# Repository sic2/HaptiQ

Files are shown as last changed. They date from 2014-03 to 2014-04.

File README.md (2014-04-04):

### HaptiQ: A Haptic Device for Graph Exploration by People with Visual Disabilities

**Student:** Simone Ivan Conte

**Supervisor:** Miguel A. Nacenta

# Project Description:

Traditional touchscreen devices do not provide any tactile feedback, being then of scarce usability for people with visual disabilities.
Miguel A. Nacenta and his team at the University of Calgary, now a Lecturer in St Andrews, developed the Haptic TableTop Puck (HTP), an inexpensive tactile feedback input device to be used on digital tabletop surfaces. Friction, height, texture, and malleability are communicated through a combination of properties of the HTP: a rod and a brake pad controlled by two servo motors, and a pressure sensor on the rod. The HTP, however, uses only one actuator on a finger to convey information to the user, which makes it unsuitable for use by people with visual disabilities, since people cannot detect directions and edges of tactile objects.

The aim of this project is to extend the HTP concept and overcome some of its limitations for its use for people with visual disabilities. The extension will consist into using multiple servo motors and rods as well as redesigning the API to support new functionalities (haptic objects, behaviours, etc).
 
My hypothesis is that the HaptiQ (pronounced Haptic cue) will facilitate the recognition of directions and edges of displayed objects. The first main objective is to create a physical prototype that is adapted for the specific needs of people with visual disabilities. 

-------------------------------------------------------------------------------

# Objectives

## Primary
    - Design and implement an haptic device for graph exploration by people with visual disabilities.
    - Develop an API to control one or more haptic devices.
    - Develop an API to easily develop WPF client applications.
    - Design and implement a new set of dynamic behaviours.
    - Design and implement a basic application for Graphs exploration.

## Secondary
    - Increase the haptic device resolution.
    - Allow the haptic device to provide audio-feedback as well.
    - Design and implement an application for simple mathematical functions exploration.

## Tertiary
    - Enable the haptic device to be used collaboratively.
    - Enable the haptic device to sense textures.

# Hardware used

- Phidgets ServoBoard and InterfaceKit
- Phidgets Servo Motors
- Pressure Sensors
- 3D-Printed models 

# Collaborating

This project is currently under alpha development and the designing is constantly changing.

Please do create a branch of the project if a new feature has to be implemented. Also, use the issue tracking on GitHub if any bug is found or new functionality is wanted.

## Getting started

Please refer to the manual to get started with the HaptiQ and the HaptiQ API

## Bugs
Whenever a bug is found please: 
- Assign a short, clear and meaningful name to the bug
- Be precise and clear
- Include only one problem per report

And follow a similar scheme

    +-------------+---------------------------------------------------+
    | Description | Describe the issue (step by step)                 |
    | Workaround  | Explain a way to temporarily solve the problem    |
    | Solution    | Explain what the solution should be               |
    | Attachments | Attach any relevant Log/Screenshot file if needed |
    +-------------+---------------------------------------------------+
    Label: bug, duplicate, invalid, etc..

# Acknoledgments

This work is supported by the School of Computer Science of the University of St Andrews and SISCA

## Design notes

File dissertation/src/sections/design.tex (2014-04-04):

\chapter{Design}

The HaptiQ aims to solve some of the problems identified in the related work. The hardware was developed using an iterative exploratory process. Therefore the design phases largely overlap with the implementation ones. The API provided has also undergone through many iterations. In this chapter I will first discuss the earliest prototypes. Then the 4-HaptiQ and the 8-HaptiQ hardware designs are illustrated. Finally, a detailed overview of the API is provided.

\section{The Hardware}
\subsection{Early Prototypes}
The hardware design of the HaptiQ has been initially based on the HTP design. Similarly to the HTP, the HaptiQ also uses mini-servos to control its actuators. However, while the HTP controls only one actuator, the HaptiQ controls four or eight of them. It immediately follows that as the number of actuators increases, so does the number of servos and the size of the device. In order to minimise the size, I designed three main prototypes by sketches (see Figure ~\ref{fig:HaptiQ-early-prototypes}). 

The first prototype extends the rotational axis in the xy plane (see Figure ~\ref{fig:first prototype}). The extension is designed as a gear that allows to choose combinations of three aligned actuators. An additional actuator would then be used to raise the selected actuators. This design reduces the number of servos, but all raised actuators will have the same height. Note that the focus of this design sketch was to minimise the number of servos, that is why actuators are shown as points, similar to Braille displays.

\begin{figure}
        \centering
        \begin{subfigure}[H]{0.5\textwidth}
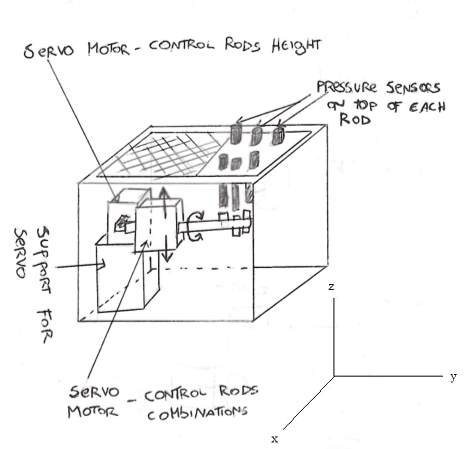
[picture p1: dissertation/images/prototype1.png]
                
                \caption{Grid based}
                \label{fig:first prototype}
        \end{subfigure}%
        ~ %add desired spacing between images, e. g. ~, \quad, \qquad etc.
          %(or a blank line to force the subfigure onto a new line)
        \begin{subfigure}[H]{0.5\textwidth}
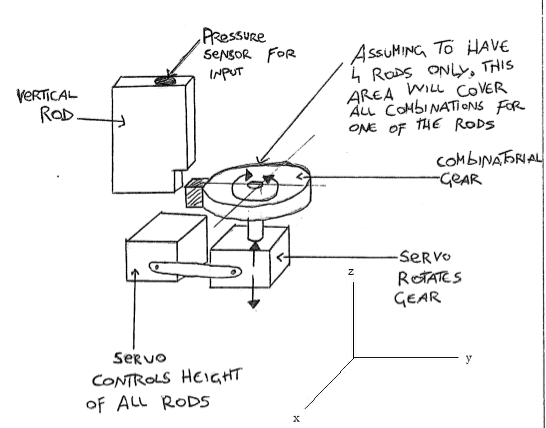
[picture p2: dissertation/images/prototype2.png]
                
                \caption{Gear based}
                \label{fig:second prototype}
        \end{subfigure}
        ~ %add desired spacing between images, e. g. ~, \quad, \qquad etc.
          %(or a blank line to force the subfigure onto a new line)
        \begin{subfigure}[H]{0.5\textwidth}
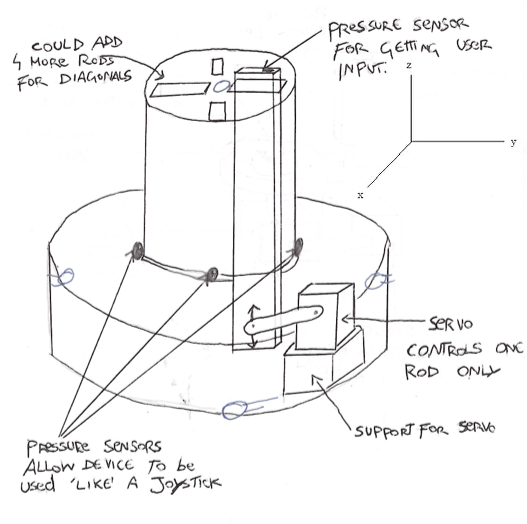
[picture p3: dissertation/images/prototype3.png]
                
                \caption{One servo per actuator}
                \label{fig:third prototype}
        \end{subfigure}
        \caption{HaptiQ early prototypes}\label{fig:HaptiQ-early-prototypes}
\end{figure}

In the second prototype I tried to minimize the total number of servos to two. One servo would be used to rotate a combinatorial gear about the z-axis (see Figure ~\ref{fig:second prototype}). A second servo can then be used to raise the first servo and all the rods. This approach can be considered very versatile and could allow an high number of actuators by keeping the number of servos always to two. Nonetheless, the actuators would all be at the same height when raised as in the first prototype. Since height can be used to convey additional information, this prototype was discarded and a third prototype was created.

The third prototype does not focus on minimising the number of servos any more, but rather on the possible functions that could be added to the HaptiQ. In this design each servo controls an actuator only and these are disposed circularly around the centre of the device (see Figure ~\ref{fig:third prototype}). The device would have a \textit{joystick} shape. Three pressure sensors could be added either at the bottom of the device or in between the internal and the external annuli. Using simple triangulation on the pressure sensors values, it could be possible to use the device like a gaming joystick and eventually augment its area of interaction. However, in one of the meetings with Saad, we realised that blind people would find this feature disrupting because understanding how far in the xy plane the device is augmented can become a challenging task. 

\subsection{4-HaptiQ}
The 4-HaptiQ is the first functional HaptiQ. This is an experimental project, with future work discussed in chapter 9, so I will occasionally refer to the device with the term prototype. This version has four actuators as shown in Figure ~\ref{fig:HaptiQ reference static actuators}. Unlike the third of the early prototypes, the main focus is on the mechanics and functions aspects.
The most successful aspect of the HTP, most probably, is the use of a small servo to mechanically move the rod along the z-axis. Nonetheless, the mechanic design used in the HTP has some flows that the HaptiQ tries to solve. The HTP, in fact, transforms the rotational motion of the servo to a linear motion only by ensuring that the servo works under a small range and that the rod slices outside the device through a small opening.
In the HaptiQ the actuators slide through a guide that allows motion only in the z-direction. In addition, each servo is linked to its actuator by using one or more screws inserted in between small openings in the actuator (see Figures ~\ref{fig:HaptiQ MinPos} and ~\ref{fig:HaptiQ MaxPos}). 

\begin{figure}
        \centering
        \begin{subfigure}[H]{0.3\textwidth}
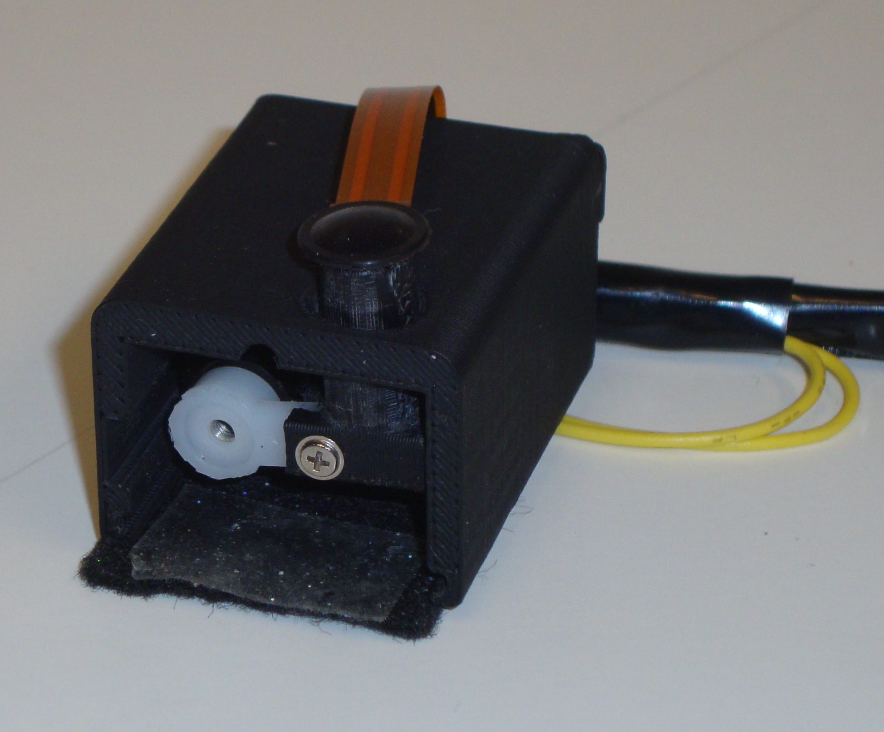
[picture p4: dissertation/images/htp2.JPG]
                
                \caption{HTP}
                \label{fig:Mechanics HTP}
        \end{subfigure}%
        ~ %add desired spacing between images, e. g. ~, \quad, \qquad etc.
          %(or a blank line to force the subfigure onto a new line)
        \begin{subfigure}[H]{0.3\textwidth}
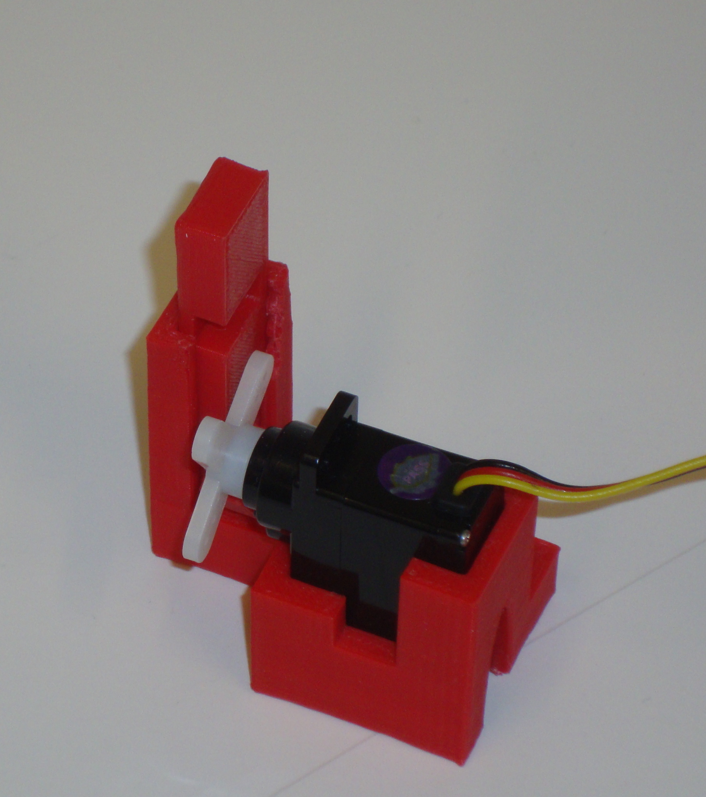
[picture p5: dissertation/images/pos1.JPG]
                
                \caption{HaptiQ MinPos}
                \label{fig:HaptiQ MinPos}
        \end{subfigure}
        ~ %add desired spacing between images, e. g. ~, \quad, \qquad etc.
          %(or a blank line to force the subfigure onto a new line)
        \begin{subfigure}[H]{0.3\textwidth}
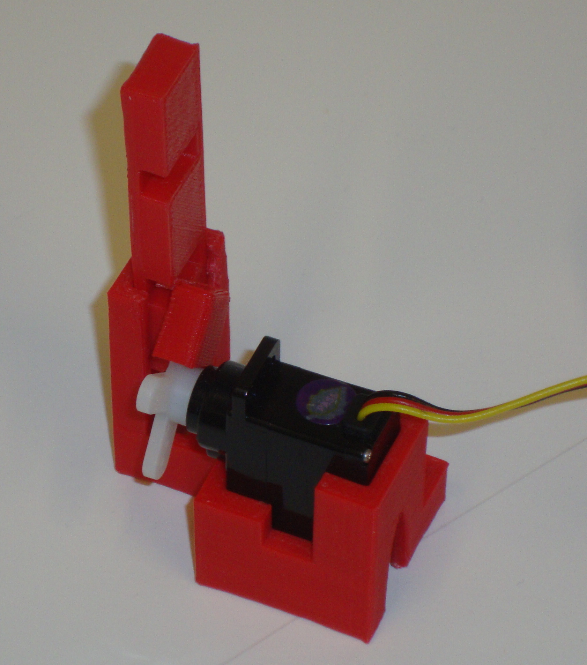
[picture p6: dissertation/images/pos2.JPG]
                
                \caption{HaptiQ MaxPos}
                \label{fig:HaptiQ MaxPos}
        \end{subfigure}
        \caption{HTP and HaptiQ actuator mechanics}\label{fig:HTP and HaptiQ actuator mechanics}
\end{figure}

This version of the HaptiQ does not provide any case. The uneven surface leads to the lack of a reference point or plane for the actuators. This is a major problem in cases where the actuators change position while the user is not currently laying his hand on the device. In fact, it follows that when the blind user places the hand on top of the device again, he or her is not able to tell what the current state of the actuators is compared to the previous one. Two solutions are provided for the 4-HaptiQ: a mid-point reference and a plane reference static actuators (see Figure ~\ref{fig:HaptiQ reference static actuators}). It is not clear which type of reference actuator works best though. My hypothesis is that the plane reference actuator should be more comfortable when using the device and provides the same functionality than the point reference actuator. 

\begin{figure}
        \centering
        \begin{subfigure}[H]{0.5\textwidth}
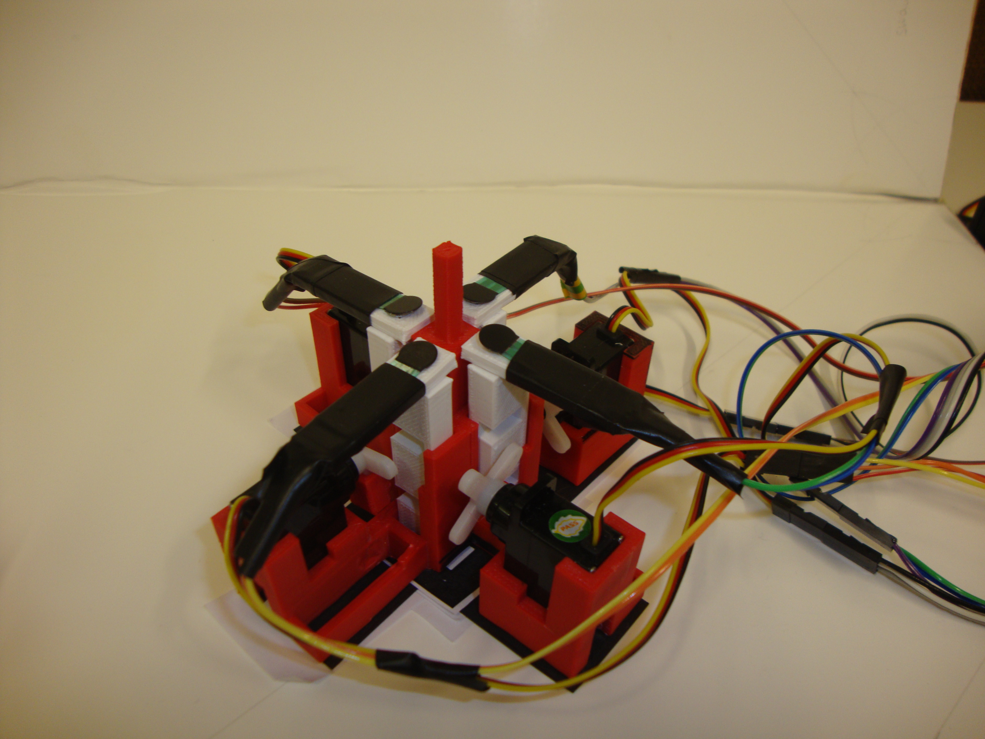
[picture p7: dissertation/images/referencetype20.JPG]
                
                \caption{Mid-Point reference actuator}
                \label{fig:Mid-Point reference actuator}
        \end{subfigure}%
        ~ %add desired spacing between images, e. g. ~, \quad, \qquad etc.
          %(or a blank line to force the subfigure onto a new line)
        \begin{subfigure}[H]{0.5\textwidth}
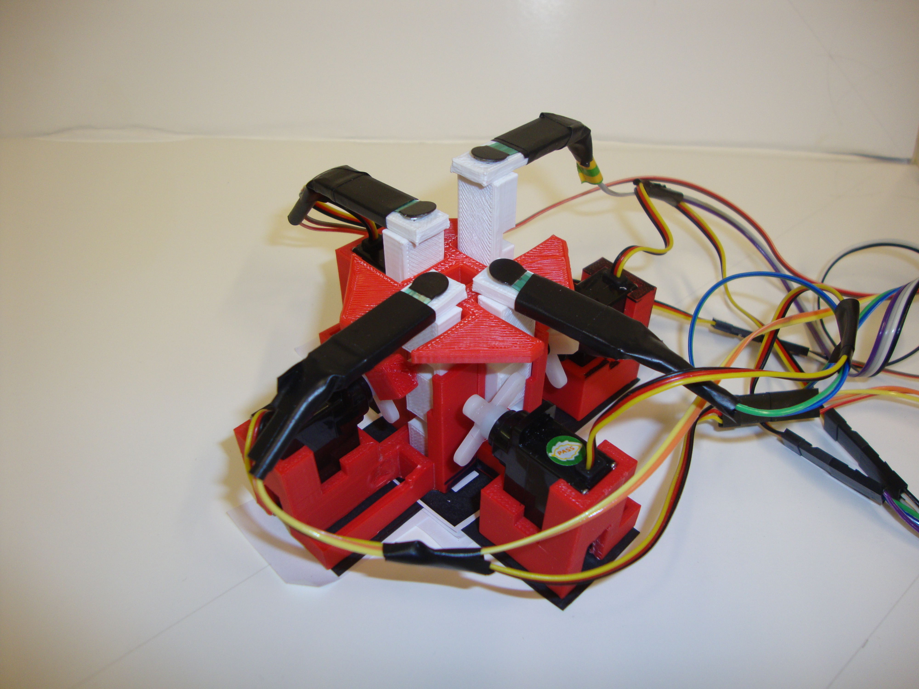
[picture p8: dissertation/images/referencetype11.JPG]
                
                \caption{Plane reference actuator}
                \label{fig:Plane reference actuator}
        \end{subfigure}
        ~ %add desired spacing between images, e. g. ~, \quad, \qquad etc.
        \caption{HaptiQ reference static actuators}\label{fig:HaptiQ reference static actuators}
\end{figure}

The HaptiQ is the first vector-based display for blind users. Whether this design provides better feedback to users or not is unknown, because no study with participants could be conducted. Therefore, the actuators are designed so to support different tops in order to be able to evaluate the HaptiQ against a point-based haptic feedback TUI. In the version here presented, only vector-like tops are provided, but other type of tops can be easily printed and fasten to the actuators.   

Finally, the HaptiQ does not have any break to simulate friction. While it could be possible to add this feature, I decided that the primary goal of this project was just to focus on the \textit{vectorisation} of the actuators. 

\subsection{8-HaptiQ}
The result of the final design iteration is the 8-HaptiQ. Using the same design of the 4-HaptiQ for eight actuators would lead to a considerable increase in size of the device. Therefore, the 8-HaptiQ has been completely re-engineered (see Figure ~\ref{fig:8-HaptiQ}). 

\begin{figure}[H]
  \centering
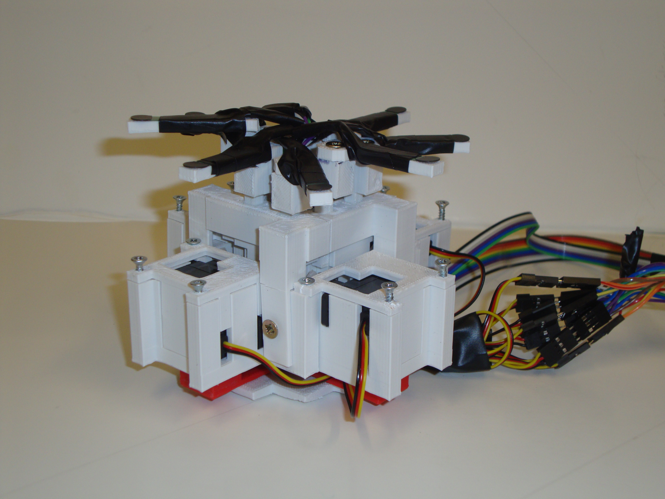
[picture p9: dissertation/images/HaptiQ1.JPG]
  
  \caption{8-HaptiQ}
  \label{fig:8-HaptiQ}
\end{figure}

The 4-HaptiQ not only is not optimised in terms of space, but its wiring is also not well engineered. As it is possible to observe in Figure ~\ref{fig:HaptiQ reference static actuators} the wiring does not allow the device to be used comfortably, especially when one wants to rotate it. 
The servos in the 8-HaptiQ are organised in couples. Unlike its predecessor, the servos are positioned horizontally (see Figure ~\ref{fig:8-HaptiQservos}) and the screws are moved more toward the centre of the rotatory mechanism of the servos. These design choices allow the device to be more compact and still preserve the same functionalities of the 4-HaptiQ. 
The device is lift up by an additional structure laying below it, allowing the wiring to be less disruptive. 

\begin{figure}[H]
  \centering
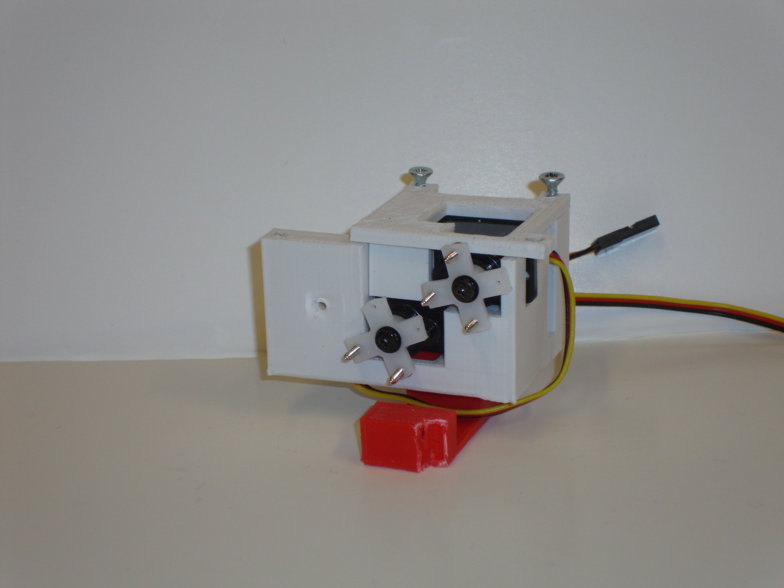
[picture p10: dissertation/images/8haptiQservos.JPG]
  
  \caption{8-HaptiQ servos couple}
  \label{fig:8-HaptiQservos}
\end{figure}

With the gathering of the wires for the sensors to the center of the device, the position of the sensors is also inverted compared to the 4-HaptiQ. While in the 4-HaptiQ the sensors meet in the middle, with this new version of the HaptiQ they are spread to the outside. It is not clear whether this design choice is an advantage or not in terms of usability. Alternatives to this solution will be provided in the near future, as discussed in the Future Work chapter.

The 8-HaptiQ takes a different approach for the design of the actuators guides. In the first version, a base was provided for the actuator, which limits this to move further down when this is at its minimum position (see Figure ~\ref{fig:HaptiQ MinPos}). But to provide an optimal wiring, the 8-HaptiQ combines the guides for all the actuators with the reference plane (see Figure ~\ref{fig:8haptiqref}). Additional connecting screws allow the actuators to be always controlled by the servos and not to fall below its minimum position. 

\begin{figure}[H]
  \centering
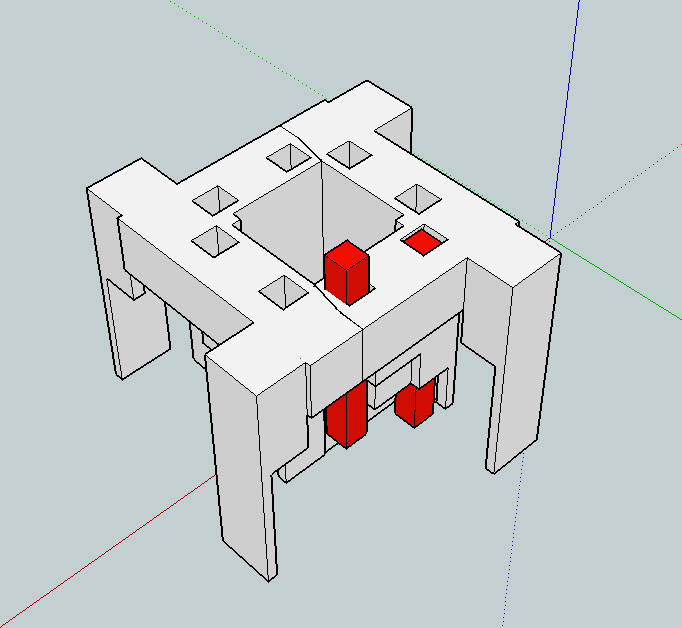
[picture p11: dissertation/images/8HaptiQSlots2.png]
  
  \caption{8-HaptiQ reference plane and actuators slots}
  \label{fig:8haptiqref}
\end{figure}

\subsection{Fiducial Markers}

The HaptiQ, like the HTP, is designed to work on interactive tabletops, specifically on Microsoft PixelSense tables (supporting Microsoft Surface SDK 2.0) \footnote{Microsoft. \url{http://www.pixelsense.com/}. [Online; last checked: 26/04/2014].}. The Microsoft Surface Bytetag is the standard fiducial marker for the PixelSense tables (see Figure ~\ref{fig:Bytetag}). But Bytetags are hard to print, if high accuracy is wanted, and expensive, if one wants to buy them from the official store.

The HaptiQ, in addition to the  Microsoft Bytetags, supports glyphs, as defined by the Glyph Recognition And Tracking Framework (GRATF)\footnote{GRATF. \url{http://www.aforgenet.com/projects/gratf/}. [Online; last checked: 04/04/2014].} (see Figure ~\ref{fig:glyph}).

Both types of fiducial markers are to be displaced on the bottom of the device, if a PixelSense table (or equivalent) is used. Otherwise, it could be possible to place a glyph on top of the device, provided that an appropriate structure is built, and recognise it using a web-cam. 

\begin{figure}[H]
        \centering
        \begin{subfigure}[H]{0.2\textwidth}
                
                \caption{Bytetag}
                \label{fig:Bytetag}
        \end{subfigure}%
        ~ %add desired spacing between images, e. g. ~, \quad, \qquad etc.
          %(or a blank line to force the subfigure onto a new line)
        \begin{subfigure}[H]{0.2\textwidth}
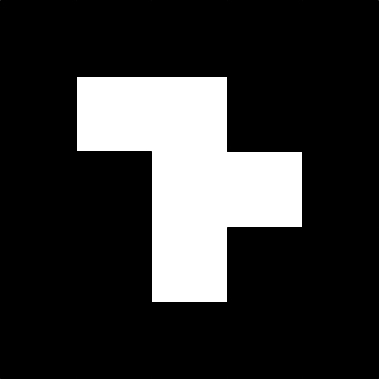
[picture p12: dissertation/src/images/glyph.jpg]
                
                \caption{Glyph}
                \label{fig:glyph}
        \end{subfigure}
        ~ %add desired spacing between images, e. g. ~, \quad, \qquad etc.
        \caption{Fiducial Markers}
        \label{fig:fiducialMarkers}
\end{figure}

\section{The API}

This section discusses the design choices taken for the API of the HaptiQ. The general idea is similar to the HapticTouch toolkit \cite{ledo2012haptictouch}. However, this has been completely redesigned to support:

\begin{itemize}
	\item multiple actuators
    \item multiple pressure sensors
    \item a completely new approach to HapticObjects and HapticBehaviours
    \item custom actions called when input is received by the user
    \item additional API to get input position of the device from different hardware
\end{itemize}

Each of these will be discussed in the following sections. 

\subsection{Overall Structure}

The API consists of two main components: the HaptiQ API used to control the device and the Input API (see Figure ~\ref{fig:api}). 
The HaptiQ API component is designed to provide high and low access to the HaptiQ. This allows the API to be versatile and to be used by beginner, intermediate and advanced developers. 
The HaptiQ API retrieves the position of the device through the Input API. 

The following two sections describe these components in more details.

\begin{figure}[H]
  \centering
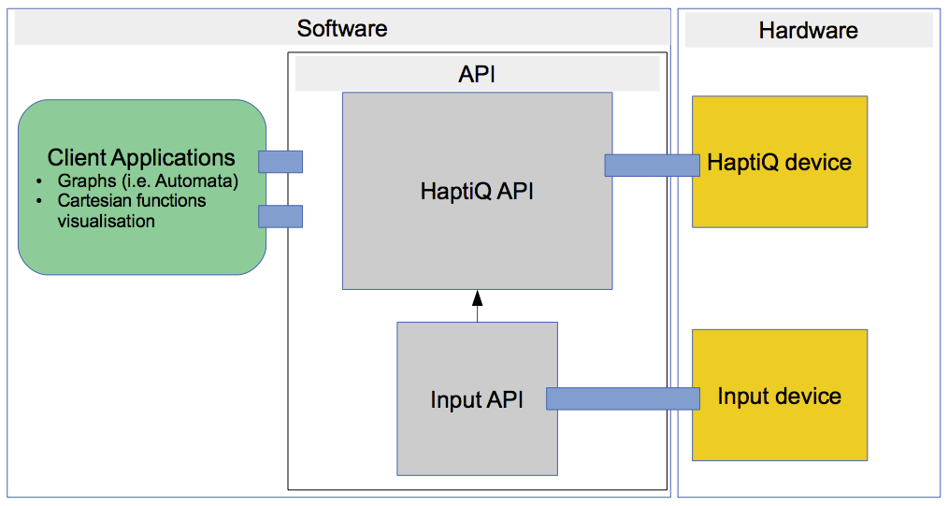
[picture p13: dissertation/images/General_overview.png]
  
  \caption{API General Overview}
  \label{fig:api}
\end{figure}

\subsection{Input API}

Initially, the HaptiQ, like the HTP, was designed to work on a Microsoft PixelSense table only.
Microsoft Surface Bytetags are located underneath the HTP to get the location of the device in the table. However, official Bytetags are expensive and printing them with a normal printer does not lead to satisfying results. In addition, the HaptiQ will be used in the near future on digital tables that do not support the Surface SDK. Therefore, in order to abstract the HaptiQ API from any hardware input dependence, a separate API component has been created (see Figure ~\ref{fig:input_api}). 

The architectural structure of the Input API is based on the classic Factory pattern. This adds a level of abstraction over the hardware that should be used to get the position of the HaptiQ. Currently the API supports Bytetags and glyphs recognition. But client applications can also add their own customised class to support different position detection methods. 

\begin{figure}[H]
  \centering
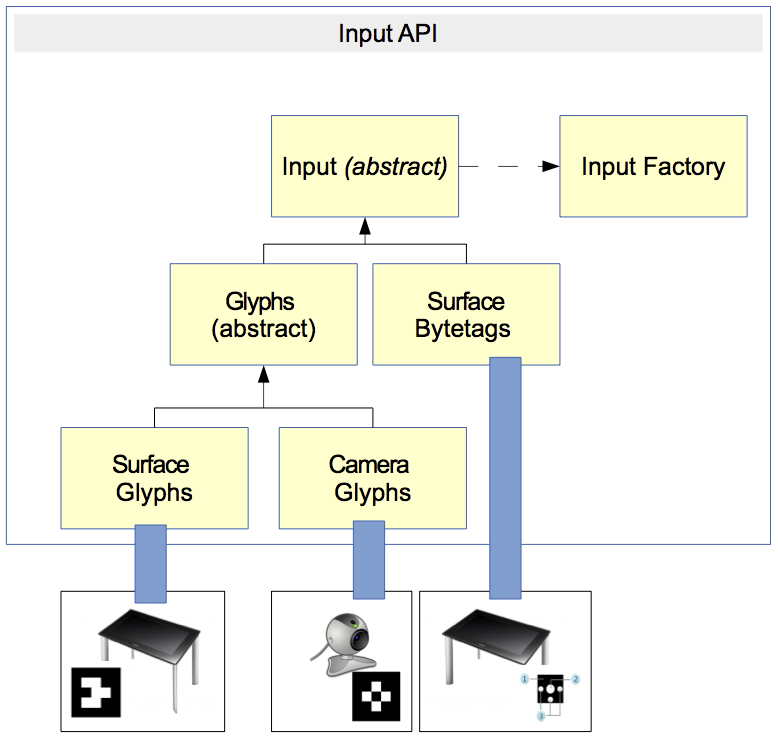
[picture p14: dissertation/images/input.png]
  
  \caption{Input API}
  \label{fig:input_api}
\end{figure}

\subsection{HaptiQ API}

The HaptiQ API plays the main role within the API by connecting the Input API, the HaptiQ device and the client applications all together (see Figure ~\ref{fig:haptiQ_api}). 

The HaptiQsManager is designed using the Singleton pattern, ensuring that only one instance exists, and controls the different parts of the internal structure of the HaptiQ API. On creation, the manager launches the configuration manager. At this stage, the API looks in the current directory for pre-saved configurations of HaptiQs. If there are not valid configurations matching the current attached devices to the machine, a configuration windows form is started, allowing users to set up devices. Otherwise, HaptiQ objects are created for each configured device. 

Each HaptiQ is a thread process on its own, which runs the current behaviours cyclically. The HaptiQ class is responsible both for controlling the actuators and getting the input via the pressure sensors. 

The manager, however, is responsible to get the devices position through the Input API. Using the observer pattern, the HapticObjects registered by the client applications are notified whenever a new input is received. If the input is relevant to a particular HapticObject, then a behaviour is returned to the HaptiQ device that caused it. 

The API allows behaviours to be added, removed, and substituted. This means that the current state of a device can be the combination of multiple behaviours. This adds an extra dimension to the haptic cues that can be transferred to the user. 

On the other hand, each HaptiQ can keep track of pressure events, without the intervention of the HaptiQsManager. Pressure data events are automatically fired to registered HapticObjects. Each HapticObject reacts differently to pressure input. 

\begin{figure}[H]
  \centering
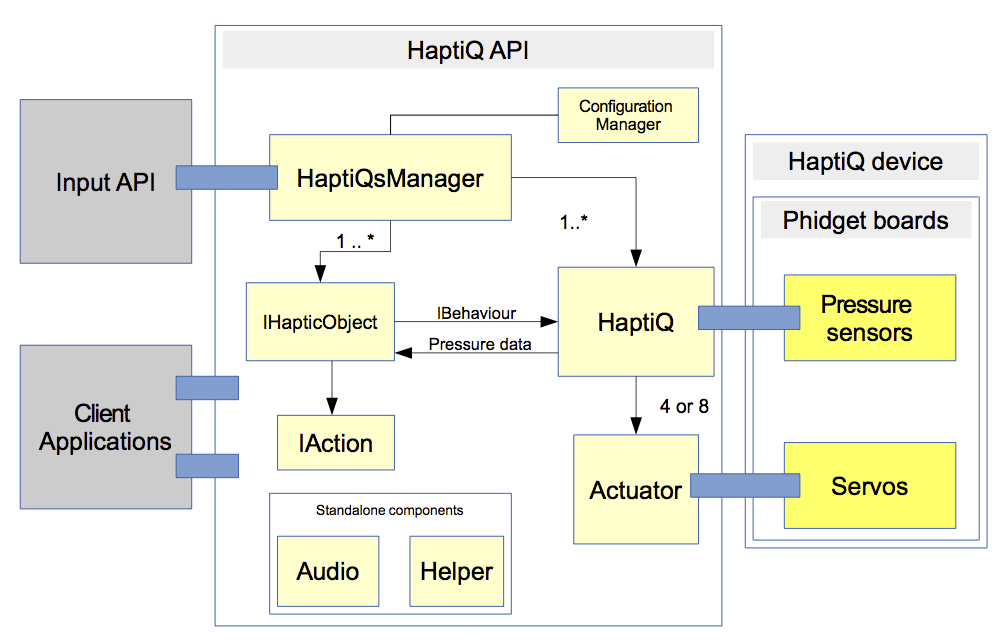
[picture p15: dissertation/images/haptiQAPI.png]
  
  \caption{HaptiQ API}
  \label{fig:haptiQ_api}
\end{figure}

\subsubsection{Haptic Objects}
Basic haptic objects are provided by the API and are designed to be used by WPF (Windows Presentation Foundation) applications without having to concern about behaviours and additional low level mechanisms. All haptic objects can carry textual information. In fact, applications should prioritise the information one wants to convey, rather than the aesthetics of the objects. Therefore, only simple shapes are provided. Obviously, one can extend the HapticShape abstract class to provide more interesting shapes, but this is outside the scope of this project.

Haptic objects are the main visual components of the client applications. Therefore, clients can also register custom actions to be run when pressure events are received by a specific object.

Figure ~\ref{fig:hapticObjects} shows examples of the haptic objects supported by the API. Rectangles and circles can be used as identity objects (e.g. nodes in a graph). Identity objects can also be linked. Links can have directions (from red to green) or not. The API allows also to specify lines and polylines. One of the example applications provided with the API, for example, uses polylines to display mathematical functions.

The used Fiducial Markers do not provide very precise input location of the device. In order to compensate, the HapticObjects provided are extended (red borders in Figure ~\ref{fig:hapticObjects}). This makes it harder to the user to leave the object, compensating for the inaccuracy of detecting the device location.

\begin{figure}[H]
        \centering
        \begin{subfigure}[H]{0.4\textwidth}
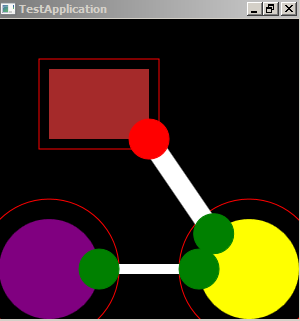
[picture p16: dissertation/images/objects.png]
                
                \caption{Identity objects and links}
                \label{fig:objects1}
        \end{subfigure}%
        ~ %add desired spacing between images, e. g. ~, \quad, \qquad etc.
          %(or a blank line to force the subfigure onto a new line)
        \begin{subfigure}[H]{0.4\textwidth}
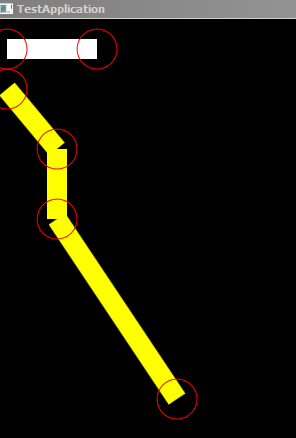
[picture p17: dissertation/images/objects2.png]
                
                \caption{Line objects}
                \label{fig:objects2}
        \end{subfigure}
        ~ %add desired spacing between images, e. g. ~, \quad, \qquad etc.
        \caption{Haptic Objects}\label{fig:hapticObjects}
\end{figure}

\subsubsection{Audio Feedback}

The audio component is a standalone one, allowing any part of the API, as well as client applications, to output beeps or textual information as audio.

While this is a small component, it still plays an important role in the API. Ungar and Blades \cite{ungar2000can} discuss whether the conjoint retention hypothesis, combining spatial and linguistic information, can provide richer haptic cueing. Their study did not show any significant improvement when adding audio feedback. However, they results were not definitive. Therefore, I decided to follow the trend of many commercial applications, like VoiceOver, which use audio to provide textual and position feedback too.

In the API provided, the Beep feedback is used only for HapticLines and HapticPolylines. The reason is that following lines is harder than identifying the existence of shapes. This approach is similar to the one taken in audio feedback applications, such as VoiceOver.

The speech synthesiser, instead, is used to read out textual information stored in the HapticObjects.

\section{Tactons}
\label{sec:designTactons} 

Pietrzak et al. \cite{pietrzak2009creating} propose a set of tactons that can be used on pin array devices and that could be used to indicate edges and directions. These tactons are designed for a $4 \times 4$ pins grid. The HaptiQ provides a maximum of eight actuators, uses lines rather than points to convey haptic cues and can provide height information as well (pin arrays typically provide only 0/1 information). Here, I present a new set of tactons. From this section on, the terms tacton and behaviour will be used interchangeably.

A tacton is used by an HapticObject to notify a device how to react when this is located on top of it. In the provided API there is a strong relationship between each HapticObject and a behaviour. Nonetheless, behaviours can be used by client defined HapticObjects or directly from a client application.

In the following sections, the scales in Figure ~\ref{fig:scales} will be used to represent the heights of the actuators.

\begin{figure}[H]
        \centering
        \begin{subfigure}[H]{0.7\textwidth}
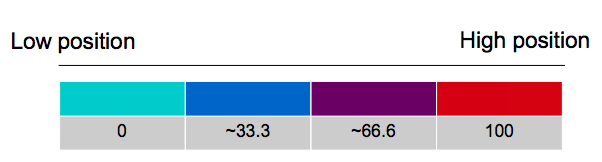
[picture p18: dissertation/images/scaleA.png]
                
                \caption{4-HaptiQ}
                \label{fig:scale-4}
        \end{subfigure}%
        ~ %add desired spacing between images, e. g. ~, \quad, \qquad etc.
          %(or a blank line to force the subfigure onto a new line)
          
        \begin{subfigure}[H]{0.7\textwidth}
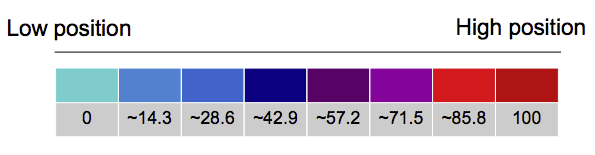
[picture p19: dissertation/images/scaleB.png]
                
                \caption{8-HaptiQ}
                \label{fig:scale-8}
        \end{subfigure}
        ~ %add desired spacing between images, e. g. ~, \quad, \qquad etc.
        \caption{Blue-Red scale used to indicate the height of the actuators in tactons diagrams. Numerical values represent the positions of the actuators in percentage}
        \label{fig:scales}
\end{figure}

\subsection{Flat and Max}

Flat and Max are the simplest tactons of the set (see Figure ~\ref{fig:Basictactons}). The Flat tacton is typically used to indicate that underneath the device there are no objects or information. The Max behaviour, instead, can be used to represent the existence of an object. For instance, when the device is inside an HapticRectangle the Max behaviour is played. 

\begin{figure}[H]
  \centering
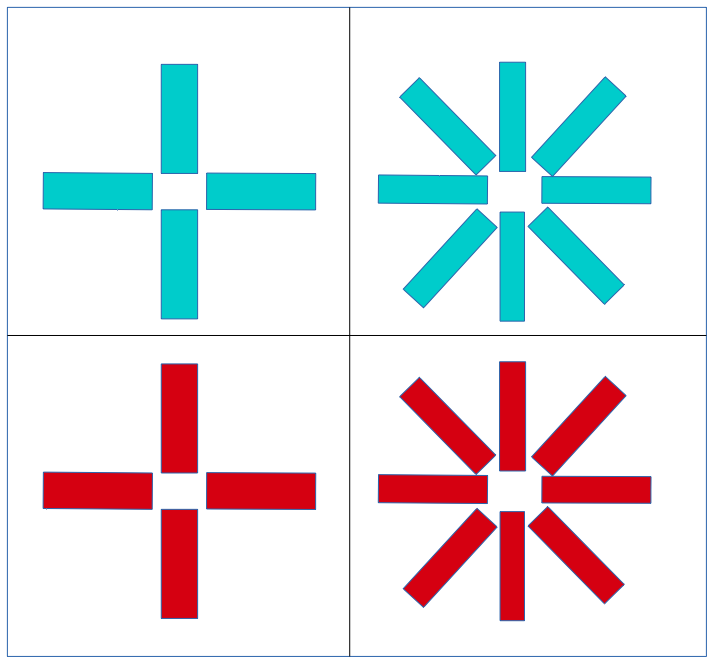
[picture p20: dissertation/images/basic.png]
  
  \caption{Basic tactons: Flat and Max}
  \label{fig:Basictactons}
\end{figure}

\subsection{Notification}
\label{sec:notification}

The Notification tacton, similarly to the Max tacton, can also be used to notify an object. In the case being, this tacton is used to notify an HapticCircle. This tacton consists into cyclically changing the positions of the actuators (see Figure ~\ref{fig:notification}). Each rod always increases or decreases its height position. But in the case the maximum or minimum height threshold is reached, the actuator direction (increase or decrease in height) is inverted.

\begin{figure}[H]
        \centering
        \begin{subfigure}[H]{0.7\textwidth}
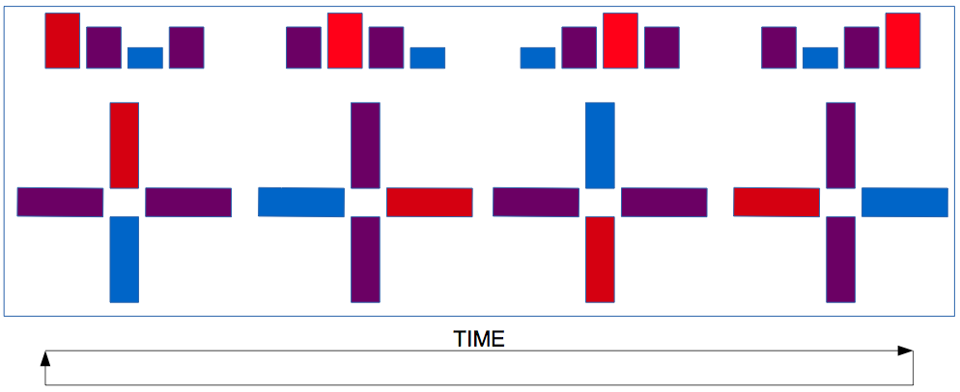
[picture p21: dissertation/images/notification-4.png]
                
                \caption{4-HaptiQ}
                \label{fig:notification-4}
        \end{subfigure}%
        ~ %add desired spacing between images, e. g. ~, \quad, \qquad etc.
          %(or a blank line to force the subfigure onto a new line)
          
        \begin{subfigure}[H]{0.7\textwidth}
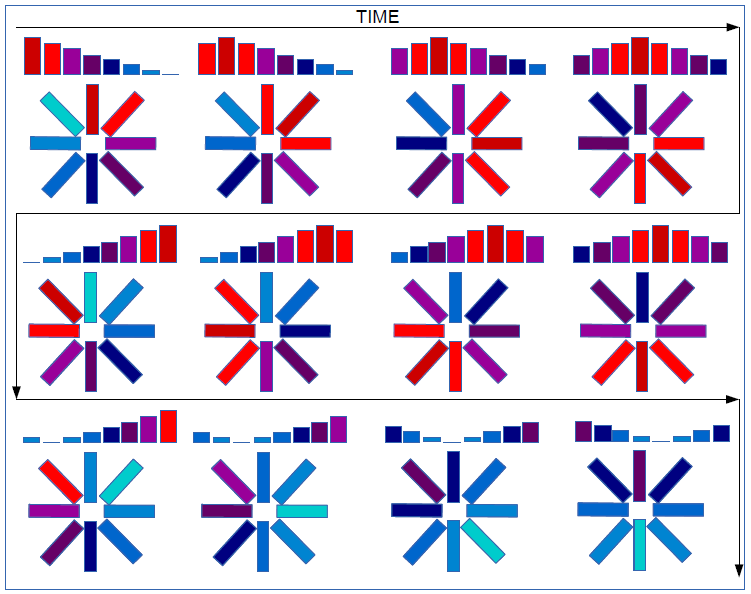
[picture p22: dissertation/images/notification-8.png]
                
                \caption{First 12 cases for 8-HaptiQ}
                \label{fig:notification-8}
        \end{subfigure}
        ~ %add desired spacing between images, e. g. ~, \quad, \qquad etc.
        \caption{Notification tacton}\label{fig:notification}
\end{figure}

\subsection{Edges and Corners}

The Edge-Corner tacton is probably the most significant one of all the tactons by allowing users to perceive edges and corners. 

Figure ~\ref{fig:edges} show how the combinations of actuators, in both the prototypes, are used to represent edges. The resolution of the device is increased by alternatively actuating adjacent actuators. It is possible to achieve a precision of 45° and 22.5° for the 4-HaptiQ and the 8-HaptiQ respectively. 

\begin{figure}[H]
        \centering
        \begin{subfigure}[H]{0.3\textwidth}
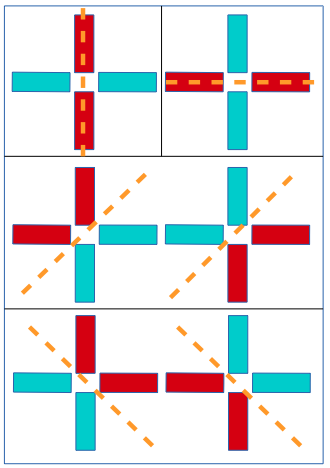
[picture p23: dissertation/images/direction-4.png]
                
                \caption{4-HaptiQ}
                \label{fig:direction-4}
        \end{subfigure}%
        ~ %add desired spacing between images, e. g. ~, \quad, \qquad etc.
          %(or a blank line to force the subfigure onto a new line)
        \begin{subfigure}[H]{0.5\textwidth}
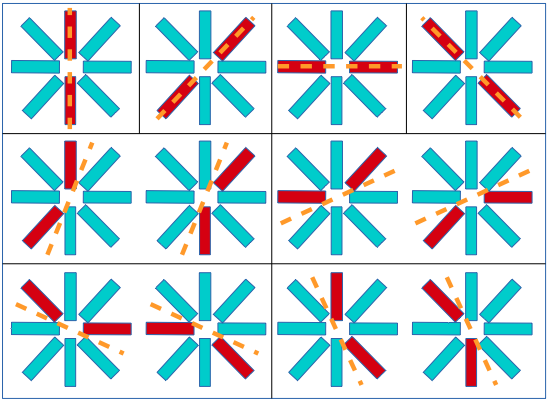
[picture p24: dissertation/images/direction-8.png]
                
                \caption{8-HaptiQ}
                \label{fig:direction-8}
        \end{subfigure}
        ~ %add desired spacing between images, e. g. ~, \quad, \qquad etc.
        \caption{Edge tacton patterns}\label{fig:edges}
\end{figure}

It is also possible to represent corners, which are merely the combinations of two edges. The 4-HaptiQ can represent corners of 90° with a precision of 45° (see Figure ~\ref{fig:corner-4}). Indeed, the 8-HaptiQ can represent corners of 45°, 90° and 135°, with a precision of 22.5° (see Figures ~\ref{fig:corner-8}, ~\ref{fig:corner-8c}). 

\begin{figure}[H]
        \centering
        \begin{subfigure}[H]{0.5\textwidth}
                
                \caption{4-HaptiQ}
                \label{fig:corner-4}
        \end{subfigure}%
        ~ %add desired spacing between images, e. g. ~, \quad, \qquad etc.
          %(or a blank line to force the subfigure onto a new line)
          
        \begin{subfigure}[H]{0.4\textwidth}
                
                \caption{8-HaptiQ}
                \label{fig:corner-8}
        \end{subfigure}
        ~ 
         \begin{subfigure}[H]{0.5\textwidth}
                
                \caption{8-HaptiQ (combinations)}
                \label{fig:corner-8c}
        \end{subfigure}
        ~ %add desired spacing between images, e. g. ~, \quad, \qquad etc.
        \caption{Corner tacton patterns}\label{fig:corners}
\end{figure}

The Edge-Corner tacton is used by the HapticRectangle, to represent its borders, and the HapticLine and HapticPolyline objects. 

\subsection{Pulsation and Linear}
The Pulsation and Linear tactons are used with the HapticLink to represent the sign of the link between two Haptic objects. Figure ~\ref{fig:pulsation} shows two cases of the pulsation tacton for the 4-HaptiQ. By symmetry it is possible to represent 8 (or 16 for the 8-HaptiQ) directions. This tacton also allows frequency to be specified, so that pulsation increases as one gets closer to the target. The static actuators in this tacton are also fundamental to identify orientation of the direction.

The Linear tacton, on the other hand, is the union of the pulsation tactons, but without any pulsation behaviour. Thus, the height of the actuators is used rather than the pulsation frequency in order to convey different information about a direction. For example, the tacton can be encoded so that the height of the actuators increases linearly as the distance between the device and the target approaches zero.

\begin{figure}[H]
  \centering
  
  \caption{Pulsation tacton patterns}
  \label{fig:pulsation}
\end{figure}

\section{Applications}

The HaptiQ can provide a new set of haptic cues which allow the visually impaired to better perceive lines, edges and directions. The two example applications shown below illustrate the types of applications that can be created using the HaptiQ API. Note that these applications have been designed as proof-of-concepts and not as applications ready to be deployed to the end users.

\subsection{Graph Visualiser}
\label{sec:graphVis}

The first application is a basic graph visualiser. The application is designed to be used by people with visual disabilities, with the assistance of a person with normal or corrected vision. The assistant can create graphs using the provided graphical user interface (see Figure ~\ref{fig:graphsVis}). Graphs contain identity objects and links as well as lines and polylines. \\
In order to create new object, the assistant has to select one of the options on the left hand side. A new window will be prompted asking for the properties of the haptic object. The procedure is the same for all the objects, except for links where the user has to select which objects to link by physically touching the objects with a finger or a bytetag. 

The design is not complete, since it does not allow objects to be deleted and graphs to be saved for later use. However, this is a good example of a possible application for the HaptiQ. One of the issues raised by Saad, in fact, is that blind people have difficulties in visualising graphs such as finite automata, trees, or network topologies. 

\begin{figure}[H]
  \centering
  
  \caption{Graph Visualiser}
  \label{fig:graphsVis}
\end{figure}

\subsection{Function Visualiser}
\label{sec:funcVis}

The second application that this project uses to prove the flexibility and usability of the HaptiQ and its API is a function visualiser. One of the most challenging tasks for the visually impaired is to be able to \textit{visualise} mathematical functions. The design of the function visualiser is also very simple. The user inputs a function, as text, and the application then evaluates and displays it (see Figure ~\ref{fig:funcVisualiser}). The application uses haptic lines and polylines to represent the functions. Cartesian axes are also added for completeness.

\begin{figure}[H]
        \centering
        \begin{subfigure}[H]{0.4\textwidth}
                
                \caption{Linear function}
                \label{fig:funct1}
        \end{subfigure}%
        ~ %add desired spacing between images, e. g. ~, \quad, \qquad etc.
          %(or a blank line to force the subfigure onto a new line)
        \begin{subfigure}[H]{0.4\textwidth}
                
                \caption{Sine function}
                \label{fig:funct2}
        \end{subfigure}
        \caption{Function Visualiser}
        \label{fig:funcVisualiser}
\end{figure}

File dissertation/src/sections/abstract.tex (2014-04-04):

\section{Abstract}

Today's technology is not as accessible for blind and visually impaired people.
Overcoming this digital divide gap for people with visual disabilities is one of today's most overlooked challenges.
Current technology provides either expensive or non-flexible devices. This dissertation investigates both commercial devices commonly used by visually impaired people, and the state of the art of haptic feedback devices.

This project presents the first vector-based display with haptic-audio feedback for people with visual disabilities: the HaptiQ. 
Two different devices of varying resolution were 3D-printed as prototypes.
In addition, a general easy-to-use API is provided together with two basic example applications. The first application shows how the HaptiQ can be used to explore simple graphs. The second program instead displays mathematical functions and is used to show how the HaptiQ facilitates edge recognition.
The sets of behaviour patterns used so far are heavily based on the use of Braille-like systems. 

With this project a new set of dynamic behaviour patterns is visually encoded in a way which favours the recognition of edges, corners and directions.

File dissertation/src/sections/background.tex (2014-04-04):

\chapter{Background}

The following chapter presents the state of the art in haptic feedback technologies and the current commercial technology for the visually impaired. The related work taken into consideration is taxonomised based on how the various techniques and devices work and how users interact with them.

Research in haptic perception and visualization has grown significantly in the last 25 years \cite{roberts2007we}. Being able to cover most of the work in haptics is not feasible. Therefore, only the most significant related work to this project will be addressed.

\section{Commercial technology for the visually impaired}
The devices and techniques currently available on the market and used by most of the visually impaired differs from what researchers have been able to achieve in the last decade. The main reason is that the most advanced technology produced by researchers is either expensive or still a prototype, or both. 

Traditional Braille and tactile maps are by far the most intuitive and easy-to-use ways to access textual and graphical information. However, these approaches are static and do not allow access to electronic devices. The resolution of tactile maps is usually low, since font size tends to be large and zoom-in actions are not allowed. Dynamic Braille displays \cite{HumanWare, shimada2010development, blindMaps} allow traditional techniques to be used for technological devices. However, only a small portion of the display can be covered using these devices and being able to keep track of the current position within the display becomes challenging.

The auditory system for blind people is probably the most important of their senses. Using the tactile system to perceive the surrounding world, in fact, can be hard to learn, especially for people who become blind in their adult stage of their life. Screen readers, like JAWS\cite{JAWS}, or auditory-aiding software, like VoiceOver\cite{voiceOver}, allow the visually impaired to explore textual information and navigate maps as well. Systems that rely just on audio feedback allow a user to follow lines and directions by emitting sounds at different frequencies. It obviously follows that a user needs to constantly explore the area around a specific point in the map in order to perceive the direction of a line or understanding the shape of an object.    
    
\section{Multimodal Interactive Maps}
An attempt to allow blind people to access geographical maps through digital devices is via multimodal interactive maps (MIMs). MIMs are input-output devices that can make use of different technologies to allow users to access or insert information (i.e Input: speech recognition, touch input. Output: audio, tactile feedback). The work presented by Broke et al \cite{brock2010usage} is the most recent type of MIM, to my knowledge. People who are visually impaired usually tend to use all their fingers when exploring objects. Therefore, enhancing multitouch input allows users to perceive maps with greater ease. Nonetheless, the maps have to be printed for each new visualisation. 

\section{Tangible User Interfaces with Mechanical Actuators}
Haptic feedback devices that use mechanical actuations are becoming increasingly popular. In fact, these are usually more flexible and adaptable to displays of different sizes. They also provide better tactile cues than audio-based techniques and MIMs.

The first device to take in consideration is the Haptic Tabletop Puck (HTP)\cite{marquardt2009haptic}, which the HaptiQ can be considered the successor of. The HTP is a simple, inexpensive and small haptic device that suits particularly well for use on digital tabletop surfaces. The tactile cue, however, is applied through one single point only. The HTP has not been designed specifically for visually impaired people. Therefore, it is not very suitable for more complex tasks such as recognising a line or a direction and follow it. 

This type of problem has been observed also with the SensAble PHANToM\cite{massie1994phantom, yu2001haptic}. Participants were asked to follow one or more lines. But the experiment showed negative results, since having only one point contact did not allowed the participants to well understand the shape of the line, especially at the end points or corners. Similarly to users of VoiceOver, blind people using the PHANToM or the HTP need to guess the direction of lines and eventually randomly explore the surrounding. 

Harrison and Hudson \cite{harrison2009providing} propose dynamically changeable physical buttons that use either pneumatic actuation or Shape Memory Materials to enhance displays with tactile feedback. This type of displays is proved to be cheap, easy to produce and effective. They are also convenient for static public displays (i.e. ATMs) or cars panel control, but not for more generic displays, such as tabletops, since specific masks need to be created for each visualisation. 

Recently the Tangible Media Group, MIT, has presented the inFORM system, a 2.5D shape display that uses mechanical actuators to provide feedback to the user\cite{follmer2013inform}. Top-down projection and a Kinect are used to provide visual feedback and acquire user input. inFORM provides excellent haptic feedback and equivalent responsiveness, nonetheless the table is bulky and expensive.

\section{Haptic Feedback by alternative mediums}

Recently Bau et al. presented TeslaTouch\cite{bau2010teslatouch} and REVEL\cite{bau2012revel}, two haptic feedback systems based on electrovibration and reverse electrovibration respectively. The purpose of these systems is to create Augmented Reality Tactile displays. These could be both extrinsic, integrated in the environment, or intrinsic, augmenting the user. A study on visually impaired people, using the TeslaTouch, has also been conducted \cite{xu2011tactile}. Participants found hard to recognise dots, as used in Braille, especially due to the fact that the tactile feedback is perceived only when the finger moves. Straight lines could be recognised, allowing some shapes be perceived (circle, square and triangle), but not with accurate precision. Another limitation of vibrotractile based devices is that it cannot be used by multiple users concurrently. 

Other techniques used to improve haptic feedback on touchscreens rely on electromagnetism. FingerFlux \cite{weiss2011fingerflux} uses magnets attached on fingertips to provide ``attraction, repulsion, vibrations and directional haptic feedback'' in a table with electromagnets pixels. The main issue related to FingerFlux is that the resolution of the display cannot be increased over a certain threshold, otherwise the electromagnets interfere with each other. In addition, FingerFlux allows to create horizontal forces, but it is not possible to render sharp surfaces.    

UltraHaptics provides multi-point haptic feedback above an interactive surface using acoustic radiation force to generate haptic cues on targets in mid-air \cite{carter2013ultrahaptics}. The system has been shown to be fairly accurate and easy to use, yet accuracy degrades quickly as the user's hand is above 200mm. 

Haptic feedback can also be transmitted by ejecting air at high pressure. AIREAL is a scalable, inexpensive and practical system that uses air to augment reality of interactive surfaces and environments \cite{sodhi2013aireal}. AIREAL works well within gaming environments and haptic cues of external environments, but the low resolution limits its use for objects and edge recognition, especially for the visually impaired.

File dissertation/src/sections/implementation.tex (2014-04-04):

\chapter{Implementation}

This chapter provides an overview of the important implementation details about the HaptiQ, as described in the Design chapter. 
Firstly, the hardware implementation is discussed, followed by the API. A dedicated section will discuss the tactons implementation. Finally, implementation details about the two example applications are covered in the last section of this chapter.

\section{The Hardware}

Building the hardware components of the two HaptiQ devices has been a challenge on its own. Both the 4-HaptiQ and the 8-HaptiQ are 3D-modelled using Google Sketchup \footnote{Google SketchUp. \url{http://www.sketchup.com} . [Online; last checked: 03/04/2014].}. Models are then exported in the STL format, a standard in CAD software, and commissioned to a 3D printer. I used a MakerBot\textregistered   Replicator\texttrademark 2x. This is an experimental 3D printer, therefore high precision (\textless 2mm) is hard to achieve and requires many attempts before being able to print the wanted model. 

Phidgets boards\footnote{Phidges. \url{http://www.phidgets.com/} . [Online; last checked: 04/04/2014].} are used to control the micro servomotors, \textit{Hitech HS-65MG}\footnote{HITECH RCD USA. \url{http://hitecrcd.com/} . [Online; last checked: 04/04/2014].}, and get pressure inputs, via force-sensing resistors. The wiring is more of a demanding task, rather than a challenging one, requiring many hours of work.

The different components of the device are assembled using super glue and screws (see the HaptiQ manual for more information on printing and assembling the device). 

\subsection{Fiducial Markers}

The provided API supports the recognition of two types of fiducial markers: Microsoft Bytetags and GRATF glyphs. The HaptiQs, built for this project, place the fiducial markers on the bottom side. However, in the case of the the GRATF glyphs, the fiducial marker can also be placed on top of the device. This is true if we assume that an appropriate structure around the HaptiQ is built, and a web-cam or similar is used to retrieve top-view images of the device with the glyph.

\begin{figure}
        \centering
        \begin{subfigure}[H]{0.3\textwidth}
                
                \caption{Raw image of Hand}
                \label{fig:rawHand}
        \end{subfigure}%
        ~ %add desired spacing between images, e. g. ~, \quad, \qquad etc.
          %(or a blank line to force the subfigure onto a new line)
        \begin{subfigure}[H]{0.3\textwidth}
                
                \caption{Raw image of 4-HaptiQ with Glyph - type 1}
                \label{fig:rawHaptiQ1}
        \end{subfigure}
        ~ %add desired spacing between images, e. g. ~, \quad, \qquad etc.
          %(or a blank line to force the subfigure onto a new line)
        \begin{subfigure}[H]{0.3\textwidth}
                
                \caption{Raw image of 4-HaptiQ with Glyph - type 2}
                \label{fig:rawHaptiQ2}
        \end{subfigure}
        \caption{Raw images}\label{fig:rawImages}
\end{figure}

The Bytetags, according to Microsoft, can be printed on standard office paper \footnote{MSDN. Printing Tagged Objects. \url{http://www.msdn.microsoft.com/en-us/library/ee804862(v=surface.10).aspx/}. [Online; last checked: 04/04/2014].}. However, during the first iteration phase of this project it was evident that printed Bytetags lead to poor results, with the fiducial markers being tracked at low frequency.

The alternative solution is to use glyphs. The Surface SDK 2.0 allows to retrieve raw image data from the interactive table. Having access to this data, it is possible to apply classical image matching algorithms to identify particular objects. This is achieved using GRATF, a C\# library that allows recognition and localization of glyphs in still images. 

Figure ~\ref{fig:rawImages} shows three raw images retrieved through the Surface SDK 2.0. The Microsoft PixelSense uses near-infrared sensors. Figure ~\ref{fig:rawHand}, for instance, represents how the hand absorbs infrared light, rather than its heat values as one may think. Glyphs are $n \times n$ grids, with n from 5 to 8, where each cell is either black or white (see Figure  ~\ref{fig:glyph}) and minimum side length of 8mm, that can be printed using Glyph Recognition Studio \footnote{Glyph Recognition Studio. Available at \url{http://www.aforgenet.com/projects/gratf/}. [Online; last checked: 04/04/2014].}. Additional rules apply, such that that the border cells can only be white and the glyph cannot be symmetrical in any of its axis. The base of the HaptiQ is covered with white paper, so that the black tiles in the glyphs are recognised more easily (see Figure ~\ref{fig:rawHaptiQ1}). However, this is not sufficient for the glyph to be recognised at all angles. After testing glyphs of different dimensions and on different surfaces, I found out that extending the glyph with low absorption material (e.g. white foam board) improves the recognition of the glyph significantly (see Figures ~\ref{fig:rawHaptiQ2} and ~\ref{fig:whitesurface}).   

\begin{figure}[H]
  \centering
  
  \caption{HaptiQ with extended white board base}
  \label{fig:whitesurface}
\end{figure}

\section{The API}

\subsection{Input API}

The Input API is the component used to retrieve the HaptiQ location on the tabletop. It follows that this is highly hardware dependent on the used hardware, especially on the type of interactive surface. The current targeted hardware comprehends the Microsoft Tabletops using the Surface SDK 2.0. Code to retrieve image data from web-cams is also provided. 
As explained in the design section, two main classes exist in the Input API: one to recognise Bytetags and one to recognise glyphs.

Recognising the Bytetags is straightforward. This is done through the \textit{TouchTarget} object of the \textit{Microsoft.Surface.Core} library. On the other hand, glyphs are recognised by calling the \textit{FindGlyphs} function, from the GRATF library, on a bitmap image. GRATF does not provide any functionality to estimate the position and the rotation of the glyphs. However, when a glyph is recognised, all its vertices are known. The position is estimated by calculating the crossing point between the two diagonals of the glyph. The rotation, instead, is estimated using the inclination angle of one of the edges of the glyph. 

The API raises events of the form:
\lstset{style=sharpc1}
\begin{lstlisting}
delegate void ChangedEventHandler(object sender, InputIdentifier inputIdentifier, Point point, double orientation, EventArgs e);
\end{lstlisting}

in order to notify the current location of a device, recognisable by a unique identifier (Bytetag or glyph). Then the HaptiQsManager, from within the HaptiQ API, handles such events.  

It is important to note that Bytetags are supported for debugging purposes only. Working with the provided tabletop is time consuming. Allowing Bytetags to be used, it is possible to run, debug and test the system using the Input Simulator provided with the Surface SDK 2.0 using a normal machine. 

\subsection{HaptiQ API}

The HaptiQ API, as previously stated, controls the device and coordinates its work with the other two main components: the Input API and the applications. The \textit{HaptiQsManager}, the \textit{HaptiQ}, and the \textit{Actuator} classes play the major role in controlling the devices and ensuring the coordination between input locations, haptic objects and behaviours. These three classes are also dependent on the Phidget library \footnote{Phidgets. Library available at \url{http://www.phidgets.com/}. [Online; last checked: 04/04/2014].}. 

On the creation of the manager, the configuration process is launched (see section ~\ref{sec:configuration} for more details about devices configuration) and HaptiQ instances are created appropriately. The manager assigns each device a unique ID, which can be used to find and access a device. 
Each HaptiQ keeps track of its own actuators, the connected pressure sensors, and the current behaviours to play. After an HaptiQ instance is initialised in the constructor, an independent thread is initiated. This consists of a loop that runs all the current behaviours every 10ms. Reducing the frequency gradually decreases the smoothness of the played dynamic behaviours. On the other hand, increasing the frequency creates an unnecessary overuse of resources. 

A behaviour consists of a dictionary mapping an actuator of the device to its wanted position. The position is expressed as a value between 0 and 1, where 0 indicates that the actuator should be moved to its minimum position, and 1 to its maximum position. The manager retrieves behaviours to be played, from each haptic object, and distributes them to the devices that generated them. Nonetheless, an HaptiQ instance allows behaviours to be explicitly added or removed, giving more flexibility to clients. Similarly to the HTP toolkit, behaviours can be combined by averaging the positions for each actuator. 
Actuators are independent from each other, therefore it is possible to exploit parallelism using a parallel for-loop as shown in Code ~\ref{lst:parallelActuators}.

The Actuator class wraps an \textit{AdvancedServoServo} from the Phidget library, used to control a single servo motor, and keeps track of the current pressure applied by the user. 

\lstset{style=sharpc1}
\begin{lstlisting}[caption={Parallelising Actuators},label={lst:parallelActuators}]
Parallel.ForEach(actuators, entry => 
                    {
                        this.setActuatorPositionByPercentage(entry.Key, entry.NormalisedPosition);
                    });
\end{lstlisting}

\subsubsection{Pressure Events}

The HaptiQ class defines two types of pressure events: pressure changes and pressure gestures. The first type of event is raised whenever the pressure registered by a sensor changes. The second type instead is raised on pressure gestures being recognised. The current API supports only one type of gesture: a \textit{press}. A press is recognised whenever the pressure registered by a particular sensor increases over a certain threshold and then rapidly decreases within a certain time frame (see Figure ~\ref{fig:pressureValues}). 

Time-series analysis could allow the recognition of other gestures, but this is outside the scope of the project.

\begin{figure}[H]
  \centering
  
  \caption{Three consecutive press gestures. Note that x-axis does not represent time.}
  \label{fig:pressureValues}
\end{figure}

\subsubsection{Haptic Objects}

Haptic objects are visual elements that client applications can use to represent information to the visually impaired. An Haptic object must implement the IHapticObject interface. This interface, as shown in Code ~\ref{lst:IHapticObject}, consists of three main methods:

\begin{itemize}
	\item \textbf{handleInput}: called whenever a new input location is received from the Input API. This method returns a Tuple of three elements: a rule to apply for the returned values (\textit{ADD}, \textit{REMOVE}, \textit{SUBSTITUTE}, \textit{NONE}) and two behaviours. For instance, the method may add a new behaviour to the HaptiQ, or substitute the current behaviour with a new one. Since HaptiQs can combine behaviours, each HaptiQ object needs to keep track of what current behaviour is assigned to each HaptiQ. 
    \item \textbf{handlePress}: called when a pressure gesture event is raised
    \item \textbf{registerAction}: allows clients to register custom actions to be executed on \textit{handlePress}. For example, a \textit{BasicAction} allows the client to specify text to be read out through the speakers when a pressure gesture is fired.
\end{itemize}

\lstset{style=sharpc1}
\begin{lstlisting}[caption={IHapticObject},label={lst:IHapticObject}]
public interface IHapticObject 
{
  Tuple<BEHAVIOUR_RULES, IBehaviour, IBehaviour> handleInput(HaptiQ haptiQ);
  
  void handlePress(HaptiQ haptiQ, PRESSURE_GESTURE_TYPE gestureType);
  
  void registerAction(IAction action);
}
\end{lstlisting}

The API provides the \textit{HapticShape} abstract class, which implements \textit{IHapticObject} and extends \textit{Shape}, from the WPF Windows Shapes. Clients, therefore, have access to haptic objects usable on WPF applications, but can also create their own custom shapes, by implementing \textit{IHapticObject}, for XNA applications. 

The \textit{HapticShape} class provides the implementation of \textit{handleInput} and provides other useful functions, such as the possibility to add textual information to a shape. The implemented \textit{handleInput} method ensures that states (\textit{UP} or \textit{DOWN}) and behaviours of a current HaptiQ, for a specific shape, are updated correctly. Classes extending \textit{HapticShape}, such as \textit{HapticRectangle} or \textit{HapticCircle}, need to implement the method

\lstset{style=sharpc1}
\begin{lstlisting}
IBehaviour chooseBehaviour(HaptiQ haptiQ);
\end{lstlisting}

which returns the behaviour that should be played by the given device, at a particular state (see Section ~\ref{sec:designTactons} for the tactons used by the provided shapes).

Finally, objects extending \textit{HapticShape} are renderable on WPF applications. These are rendered only when the object is added to a canvas or grid within the client application.

\section{Configuration}
\label{sec:configuration}

The two prototypes created in this project have different characteristics. For instance, the second version has eight actuators, rather than four, and its servos have a certain action range that the first version does not have. The API allows devices with different characteristics to be used by serializing their configurations as XML files. On creation, the manager inspects the current directory for XML configuration files\footnote{Pattern used to name configuration files is: 'CONFIG\_*.xml'} and attempts to create HaptiQs using the deserialized configurations and the attached Phidget boards.  

But even so, it could be the case that no configuration file exists for an attached HaptiQ. This is especially true the first time a device is used. In this eventuality a configuration form is prompted to the user (see Figure \ref{fig:configurationPanel}). The form has been created using \textit{WinForms}, so that no dependency on WPF or similar library is added. The panel allows users to specify which actuators to use, their range of action, whether to use pressure input or not, and the fiducial marker to use. 

Users are prompted with a configuration form until all attached Phidget boards are configured.

\begin{figure}[H]
  \centering
  
  \caption{Configuration Form}
  \label{fig:configurationPanel}
\end{figure}

\section{Tactons}

Tactons, or behaviours, represent the way the actuators of the HaptiQ move to represent shapes, edges, and directions. This section gives an overview of the behaviours implementation.

Each behaviour must implement the play method:

\lstset{style=sharpc1}
\begin{lstlisting}
abstract Dictionary<int, double> play();
\end{lstlisting}

which returns a dictionary mapping actuators to their desired positions. 
This is the only requirements that has to be satisfied whenever a new behaviour is created. In addition, tactons can be dynamic. Therefore, the \textit{Behaviour} abstract class provides an internal timer that behaviours should update at each call to \textit{play}. 

Being able to map an HaptiQ to basic behaviours, such as \textit{Flat} and \textit{Max}, is fairly simple because there is no dependence on previous states of the behaviour or the position and orientation of the device relative to a segment (e.g. Pulsation behaviour). The initial approach consisted in hard-coding all possible cases as shown in Code ~\ref{lst:tactonsInitialApproach}. This example is valid only for the 4-HaptiQ. It becomes clear that as the number of actuators increases, the code will also increases in size and eventually becomes unmaintainable. 

\lstset{style=sharpc1}
\begin{lstlisting}[caption={Tactons - Initial approach},label={lst:tactonsInitialApproach}]
private int[][][] directionMatrix = new int[][][]
                    {  new int[][]{                 // vertical 
                        new int[]{0, 1, 0, 1, 0}, 
                        new int[]{1, 1, 1, 0, 0}, 
                        new int[]{0, 0, 1, 0, 1}, 
                        new int[]{1, 1, 0, 0, 1}, 
                        new int[]{0, 1, 0, 1, 0}, 
                        new int[]{1, 1, 1, 0, 0}, 
                        new int[]{0, 0, 1, 0, 1}, 
                        new int[]{1, 1, 0, 0, 1}}, 
                    new int[][]{                    // horizontal
                        new int[]{0, 0, 1, 0, 1},
                        new int[]{1, 1, 0, 0, 1},
                        new int[]{0, 1, 0, 1, 0},
                        new int[]{1, 1, 1, 0, 0},
                        new int[]{0, 0, 1, 0, 1},
                        new int[]{1, 1, 0, 0, 1},
                        new int[]{0, 1, 0, 1, 0},
                        new int[]{1, 1, 1, 0, 0}},
                   ...
                   };
\end{lstlisting}

The second approach generalises the initial approach, by representing actuators as bits, rather than integers within arrays, and applying bitwise operations (see Figure ~\ref{fig:bits}). 

For example, to represent a vertical line in the 4-HaptiQ, we can just use the number five:

		0101 (5) = 0001 (1) \& 0100 (4) \\
Shifting numbers to right (or left) with carry allows behaviours to choose what actuators to use. 
The shifting offset is based on the orientation of the device compared to the segment it has to represent. Finding this value consists into subdividing the HaptiQ in logical sectors. For instance, the 4-HaptiQ is divided in eight sectors (see Figure ~\ref{fig:sectors}). Even sectors, in red, represent states that the device needs to represent by alternating actuators over time.

Say that 0101 is valid for the first sector, then when the device is in the third sector a shift by one only is needed: $0101 \gg 1$ = 1010 (with carry). For the case of even sectors, bits are not ended, but applied conditionally on the internal timer value:

		0001 (timer mod 2 == 0)
        
        0100 (timer mod 2 != 0)

\begin{figure}[H]
  \centering
  
  \caption{Actuators bits representation}
  \label{fig:bits}
\end{figure}

\begin{figure}[H]
  \centering
  
  \caption{4-HaptiQ sectors}
  \label{fig:sectors}
\end{figure}

Similar bitwise operations, as described above, are applied for the direction, pulsation, and linear tactons. The notification tacton, however, takes a different approach since each actuator can be in different states (see Section \ref{sec:notification}). The solution used is to use a 2-D array with values $[position, direction]$ for each actuator, where the direction indicates whether the position should increase or decrease in the current iteration. The direction is inverted when the minimum or maximum allowed position is reached.  

\section{A basic example}

In this section, I will show how to use the API using a simple example (see Code ~\ref{lst:basicAPIUsage}). This section is necessary to properly understand section ~\ref{sec:Applications}, which discusses the provided example applications of this project.

The first step consists in creating a WPF application and adding a reference to the HaptiQ\_API. In the design view, add a Grid named \textit{container} to the main window. Import the HaptiQ\_API in the code view of the application. 

The call \textit{HaptiQsManager.Create(windowTitle, \textless Input Class\textgreater)} initialises the HaptiQ device and the Input API, using the specified Input class (e.g. 'SurfaceInput' for Bytetags). 
Objects are automatically added to the system when they are created. These are rendered only when added to a WPF grid or canvas. 

In the \textit{OnClosed} method of the WPF application, it is important to call \textit{HaptiQsManager.Instance.delete()} to ensure that the HaptiQs are detached correctly and all resources are disposed correctly.

\lstset{style=sharpc}
\begin{lstlisting}[caption={Basic API usage},label={lst:basicAPIUsage}]
using HaptiQ_API;

public partial class Application : SurfaceWindow
{
  public Application()
  {
      HaptiQsManager.Create(windowTitle, ''SurfaceInput'');
      
      HapticShape rect0 = new HapticRectangle(50, 50, 150, 200);
      rect0.color(Brushes.Salmon);
      this.container.Children.Add(rect0);
      
      HapticShape rect1 = new HapticRectangle(150, 350, 200, 200);
      rect1.color(Brushes.Orange);
      this.container.Children.Add(rect1);
      
      HapticShape rect2 = new HapticRectangle(550, 150, 100, 100);
      rect2.color(Brushes.Green);
      this.container.Children.Add(rect2);
      
      HapticShape link = new HapticLink(rect2, rect1, true);
      link.color(Brushes.White);
      this.container.Children.Add(link);
  }
  
  protected override void OnClosed(EventArgs e)
  {
      base.OnClosed(e);
      HaptiQsManager.Instance.delete();
      Application.Current.Shutdown();
  }
}
\end{lstlisting}

\begin{figure}[H]
  \centering
  
  \caption{Basic API usage}
  \label{fig:basicexample}
\end{figure}

Please refer to the HaptiQ manual for further details and additional examples on how to use the API. 

\section{Applications}
\label{sec:Applications}

This section will briefly explain some of the implementation details about the two example applications provided with this project. 

\subsection{Graph Visualiser}

The graph visualiser application, as explained in section ~\ref{sec:graphVis}, provides basic functionality to build and visualise graphs that can be perceived using the HaptiQ. 
The main user interface is created using Visual Studio to organize the WPF standard controls (i.e. buttons). A click handler is attached to each button. Two types of buttons exist in the application. The first type are used to create new haptic objects, while the second one to make the objects selectable or not. \\
When the first type of buttons is used, a new window is shown allowing the user to choose the properties of the haptic object. A create button in the new window adds the haptic object to the main window, as shown in Code ~\ref{lst:basicAPIUsage}.
The second type, instead, iterates over all the haptic objects through the \textit{HaptiQsManager} and make them selectable or not. This functionality is useful because we want objects to be selectable only when creating the graph and not when the user is sensing it.  

\subsection{Function Visualiser}

The function visualiser application is self-contained in one simple C\# class. A user can input basic functions (e.g. linear, trigonometric) via the interface provided by the application. The interface, similarly to the Graph Visualiser one, is created with the assistance of Visual Studio. \\
The application accepts only functions of the form: $ y = f(x) $, with only one occurrence of x. Functions are evaluated using the NCalc library \footnote{NCalc. Library Available at \url{http://www.ncalc.codeplex.com/}. [Online; last checked: 02/04/2014].} at regular intervals over x. The pseudocode ~\ref{lst:functVisPseudo} shows the use of the NCalc library and the creation of the HapticPolyline. 

\lstset{style=sharpc1}
\begin{lstlisting}[caption={Function Visualiser pseudocode},label={lst:functVisPseudo}]
var regex = new Regex(Regex.Escape("x"));
for(int i = 0; i < RANGE; i++)
{
  var function = regex.Replace(inputTextFunction, i.ToString(), 1);
  NCalc.Expression expr = new NCalc.Expression(function);
  var y = expr.Evaluate();
  points.add(new Point(i, y));
}

HapticShape polyline = new HapticPolyline(points);
polyline.color(Brushes.White);
container.Children.Add(polyline);

\end{lstlisting}

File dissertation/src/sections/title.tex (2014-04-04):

\begin{titlepage}
\begin{center}

% Upper part of the page. The '~' is needed because \\
% only works if a paragraph has started.

% Title
\HRule \\[0.4cm]
{ \huge \bfseries HaptiQ: A Haptic Device for Graph Exploration by People with Visual Disabilities }
\HRule \\[0.4cm]

 %~\\[1cm]

% Author and supervisor
\begin{minipage}{0.4\textwidth}
\begin{flushleft} \large
\emph{Author:}\\
Simone Ivan \textsc{Conte}
\end{flushleft}
\end{minipage}
\begin{minipage}{0.4\textwidth}
\begin{flushright} \large
\emph{Supervisor:} \\
Dr.~Miguel A. \textsc{Nacenta}
\end{flushright}
\end{minipage}

\vfill

% Bottom of the page
{\large \today}

\end{center}
\end{titlepage}

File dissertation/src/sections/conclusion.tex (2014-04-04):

\chapter{Conclusions}

Technology, in the last decade, has become increasingly ubiquitous. However, little effort has been spent on enabling the digital world to be used by people with disabilities. Blind people, in particular, have to face considerable difficulties when accessing textual and visual information. While screen readers are able to convey textual information with a good degree of success, the same is not true for data with a more graphical nature. Researchers are exploring haptic feedback technologies, allowing the blind to perceive shapes and textures, but low flexibility and high cost are still a main concern.  

This project presents the HaptiQ, an inexpensive haptic-audio feedback device that the visually impaired can use on interactive surfaces to explore both textual and graphical information. The main focus of the HaptiQ is to facilitate the blind to sense edges, corners and directions.

All the main objectives of this project have been achieved. Two prototypes have been created, an API provides both low and high level control over the device, and two example applications show some practical uses. This work presents novel approaches in the area of haptic feedback technology. The HaptiQ, to the best of my knowledge, is the first vector-based haptic feedback display for the visually impaired. No user study has been conducted to formally evaluate the performance of the device. However, informal observations have given positive feedback. The device also provides audio feedback, adding an additional dimension that users can perceive.

The HaptiQ uses a new set of dynamic tactons to convey information to the visually impaired. Tactons are ``structured, abstract, tactile messages which can be used to communicated information non-visually''\cite{brown2005first}. The tactile encoding used by the HaptiQ is strongly driven by the design of the device itself. The main emphasis, on designing both the device and the tactons as well, was to facilitate the recognition of edges, corners and directions by the visually impaired. 

This work has some limitations that will be addressed in the next versions of the HaptiQ. The first issue to address will be to re-engineer the device in order to decrease its size. A smaller device could allow many users to collaborate using the same interactive surface. Friction and texture are two dimensions that have not been explored due to time constraints. Nonetheless, these properties could open new unexplored perspectives.   

Moreover, the project opens to new areas of further research. A study targeting the usability and performance of the device itself would help the next development phase to produce a device closer to a final product. In addition, Régis Ongaro-Carcy and Dr Miguel A. Nacenta are currently working on building a strategic game for the visually impaired that makes use of the HaptiQ. A user study will evaluate how well the device performs when used collaboratively in a gaming environment. I have passively assisted the project by adapting both the hardware and the API to their needs. But, I am planning to actively contribute in the design and implementation of the game as well. 

Finally, the biggest contribution of this project has been trying to bridge the digital divide gap for the blind. This work will be released under the GNU General Public License allowing the visually impaired to make their own haptic device and applications at home, with a low budget. The HaptiQ is not a final product yet, but I am planning on improving both the hardware and the software components as a personal side project.

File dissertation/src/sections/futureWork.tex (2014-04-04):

\chapter{Future Work}
\label{chap:futureWork}

The HaptiQ aims to take the Haptic Tabletop Puck to the next level, by allowing the visually impaired to sense edges, corners and directions, and still keeping the hardware inexpensive. In the future, I plan to pursue additional work in collaboration with Régis Ongaro-Carcy, Saad Attieh, and Dr Miguel A. Nacenta. This chapter intends to highlight the potential work that could be planned for the near future, as well as the work currently pursued by Régis Ongaro-Carcy and Dr Miguel A. Nacenta. 

One of the aims of this project is to distribute this work under the GNU General Public License. We believe that the HaptiQ can facilitate blind people to use interactive surfaces without having to spend a considerable amount of money and still providing a sufficient haptic-audio feedback quality. 
The next iteration of the HaptiQ will focus on improving the design and mechanics of the device. The current version is easy to print, but requires about 10 hours of assembling. It is important to redesign some of the pieces and part of the structure of the device, making the HaptiQ more modular and easy to access to people with no experience with 3D printing and models construction. 

In this work no user study was conducted. While the HaptiQ seems to perform very well, it is still unknown how helpful the provided tactons are. A user study with people with visual impairments could help understand how the design, mechanics, and tactons of the HaptiQ perform. Whether a vector-based haptic feedback display provides more helpful cues to the blind and visually impaired when following a line, or on recognising a corner, is unknown. The current device supports modular actuators, so it is possible to compare the vector-based HaptiQ with a grid-based one. A study analysing the current HaptiQ will help to understand how well the current device performs and what is to be improved, added, or removed in the next iteration phase. For instance, it would be very interesting to compare technology similar to VoiceOver \cite{voiceOver}, that uses audio feedback only, with the HaptiQ that uses both haptic and audio feedback (or haptic only). An improved version of the function visualiser application, for instance, would help understanding how well blind people can follow lines using the HaptiQ.  

Future work will consist into exploring what new features should be added to the HaptiQ and its API. New types of haptic objects and behaviours could make the API more powerful, allowing client applications to describe more scenarios. The use of electro-vibration and/or mechanical vibrations could allow the HaptiQ to sense textures. This would be a powerful feature, since the aim of HaptiQ is to compensate for the flat and haptic-less interactive surfaces. Adding a break, like the HTP \cite{marquardt2009haptic} does, would add a new dimension to the HaptiQ: friction. Providing resistance to movements parallel to the used surface can allow applications to represent certain types of textures. There are also other possibilities. For example, different meanings can be given to objects that exert different opposing forces to the movement of the HaptiQ. 

Currently, Régis is developing a strategic game, based on geographical information, for visually impaired people. He is working under the supervision of Dr Miguel A. Nacenta and will conduct a user study with visually impaired people at the Université de Toulouse. While he is working on his research, I will provide support with the HaptiQ, being the main developer. I am also planning to actively participate in the design and development of the game, with the permission of Régis and Dr Nacenta.

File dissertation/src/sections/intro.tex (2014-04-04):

\chapter{Introduction}
The use of technology for the blind and the visually impaired is not obvious. The digital divide gap is significant and has an evident impact not only on the life style of the visually impaired, but also on how they interact with others and the surrounding environment. This can lead to one's exclusion from society. Therefore, presenting information in a correct, fast and easy-to-access manner to the visually impaired is a fundamental challenge in a world where technology evolves at an exponential rate. \par

So far, Braille can be considered the most used form of tactile graphics since the XIX century\cite{andrea2009history}. Braille is a coding system for alphanumeric symbols, with each braille character being a combination of raised dots or tactile bumps positioned within a fixed grid. While Braille has been shown in the past to be excellent for textual information, the trend is changing. In fact, touch screen devices, which are becoming always more pervasive, do not allow Braille to be reproduced. \par

In addition to the technology revolution we are experiencing, nowadays, the amount of data  daily produced is increasing. Most of the time it is not feasible to represent data and its information in textual form, whether it is a small data set or big data. Therefore, in the last couple of decades data visualisation has been playing a crucial role in many areas, such as economics, physics, and chemistry aiding scholars and professionals to better understand problems and show their results to the public. Graphical visualisation can also help users to better understand more abstract concepts, such as graphs (e.g. automata, trees, etc) and functions behaviour. 
The progress in information visualisation and presentation has been substantial in the last 20 years, with the increase in computational power and larger displays. However, this progress has not had a similar strong positive impact on the way the visually impaired interact with technology. \par 

It is then necessary to undertake such challenge in order to minimise the digital divide for the visually impaired. Traditional devices include screen readers, like JAWS\cite{JAWS}, and dynamic Braille displays\cite{HumanWare, shimada2010development, blindMaps}. However, these tools are generally very expensive, bulky and lack of flexibility and adaptability. For instance, screen readers cannot be used for graphics, while dynamic displays can represent only a small portion of a display and being able to locate their relative position can become very hard.
Currently researchers and industry are increasing their effort toward bridging this gap. This project is based on the work of Marquardt et al.(2009)\nocite{marquardt2009haptic}, who developed the Haptic Tabletop Puck (HTP), an inexpensive tactile feedback input device to be used on digital tabletop surfaces. Friction, height, texture, and malleability are communicated through a combination of properties of the HTP: a rod and a brake pad controlled by two servo motors, and a pressure sensor on the rod. The HTP, however, uses only one actuator on a finger to convey information to the user, which makes it unsuitable for use by people with visual disabilities, since directions and edges of tactile objects cannot be detected with ease. \par

Here I present the HaptiQ (pronounced Haptic Cue), a Tangible User Interface (TUI)\cite{ishii1997tangible} with tactile and audio feedback input which takes the HTP to the next level for people with visual impairments. In addition an easy-to-use API and a new set of dynamic Tactons is presented. Tactons are ``structured, abstract, tactile messages which can be used to communicate information non-visually''\cite{brown2005first}.\par
This project will be available to download under the GNU General Public License in accordance to one of the aims of the project: building an accessible, inexpensive and easy-to-build device for the visually impaired. \par

\section{Contributions}

The contributions of this project can be summarised as follows:
\begin{itemize}
	\item Create an inexpensive haptic-audio feedback device for the visually impaired
    \item Create a device that can be 3D-printed at home
    \item Create a modular device, allowing further studies to explore different types of tactons
    \item Design and implement a dual-API (both high and low level) for the device which is easy-to-use
    \item Project available to the community under the GNU General Public License 
\end{itemize}

\section{Report Outline}
The remainder of this report is structured as follows. \textbf{Chapter 2} states the overall objectives of this project in order of importance and relevance. In \textbf{Chapter 3} a detailed overview of the related work is presented, in order to get a flavour of the current state of the art and how this project fits in it. The research techniques and methodology used through the development phase of this project is described in \textbf{Chapter 4}. \textbf{Chapter 5} addresses any ethical considerations. The design and implementation aspects of the HaptiQ, the API and other aspects of this project are described in \textbf{Chapters 6, 7}. The current work is evaluated in \textbf{Chapter 8}  and future work in \textbf{Chapter 9}. Finally \textbf{Chapter 10} provides a conclusive summary of this project.

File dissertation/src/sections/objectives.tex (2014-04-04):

\chapter{Objectives}

\begin{enumerate}
	\item Primary
    \begin{enumerate}
    	\item Design and implement an haptic device for graph exploration by people with visual disabilities.
        \item Develop an API to control one or more haptic devices.
        \item Develop an API to easily develop WPF client applications.
        \item Design and implement a new set of dynamic behaviours.
        \item Design and implement a basic application for Graphs exploration.
    \end{enumerate}
    \item Secondary
    \begin{enumerate}
        \item Increase the haptic device resolution.
        \item Allow the haptic device to provide audio-feedback as well.
        \item Design and implement an application for simple mathematical functions exploration.
    \end{enumerate}
    \item Tertiary
    \begin{enumerate}
    	\item Enable the haptic device to be used collaboratively.
        \item Enable the haptic device to sense textures.
    \end{enumerate}
\end{enumerate}

All the primary and secondary objectives have been achieved.\par
The secondary objectives, in semester one, included also the implementation of dynamic pointing. This feature, however, was removed for reasons discussed later in the Evaluation chapter.

In addition to the objectives above, I pursued this project with the following other goals in mind:
\begin{itemize}
	\item Investigate and evaluate the current state of the art.
    \item Develop a device which fits within the current state of the art.
    \item Develop a modular device which can be easily adapted to various conditions and needs.
\end{itemize}

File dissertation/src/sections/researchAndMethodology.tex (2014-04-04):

\chapter{Research and Methodology}

The nature of this project is more research than engineering oriented. It follows that common software development practices, such as SCRUM, were not used. Instead, the development process was articulated in three main phases: background research, hardware and software investigation, and hardware and software development. Each of these phases will be discussed below. 

\section{Project phases}
The background research phase was necessary to understand what the current state of the technology in haptic devices is. This phase was run mainly in the first two months of the project. 

The hardware and software investigation phase consisted in getting familiar with the 3D Printer, the Phidgets API and exploring what possible hardware could be used. For instance, hardware experimentation on Quantum Tunnelling Composite (QTC) was pursued to get pressure input from the device. The final evaluation was negative due to the reduced size of QTC tiles, which do not allow an easy installation on the HaptiQ. I then decided to use basic a Force-Sensing resistor instead. 

The hardware and software development phase followed the investigation phase logically, but not necessarily temporarily. Both the hardware and the software presented in this report are the product of an iterative exploratory design process. Weekly meetings with the supervisor were arranged. Each meeting consisted in reporting the work done in the previous week, planning the work for the week after and discussing design problems and features. These brainstorming meetings were fundamental in order to achieve the final HaptiQ.

Monthly meetings with Saad Attieh were arranged to discuss various design choices and get direct feedback from a blind person, which I found invaluable. 
One of the aims of this project is to develop an haptic device easy to build with an easy-to-use API. On the software side, the API has been designed having in mind that the code will be used for future work. Therefore, I wrote extensive XML documentation for the API calls and provided abstract instances, where necessary, to allow future users to extend the API. The attached manual contains a basic usage example of the API and the list of the required hardware components to 3D print and assemble the HaptiQ. 

\section{Management software}
Version control systems have been used to facilitate the software development of the API and maintain the 3D models of the HaptiQ always up-to-date. The Mercurial version control system, managed by the School of Computer Science, has been used from the beginning of the project until almost the very end. On the \nth{18} March 2014, with Régis Ongaro-Carcy joining the project, I decided to switch to GitHub \footnote{GitHub. \url{http://www.github.com/}. [Online; last checked: 03/04/2014].}. The main reasons behind this choice are that Régis does not have access to Mercurial repositories within the School of Computer Science and GitHub provides an issue tracking system that facilitates project work with more than one person.  

At the start of the project I used the issue tracker Bugify \footnote{Frondiz. Bugify. \url{http://www.bugify.com/}. [Online; last checked: 27/03/2014].}. However, later in the project development process I stopped using this tool because the project evolved too quickly and Bugify slowed down my process rather than speeding it up. 

\section{Testing}
One of the most challenging parts of this project was testing. Being the implemented API highly dependent on both the HaptiQ device (Phidget boards, servos, and pressure sensors) and the input device (table, camera, et cetera) the amount of Unit testing was minimal. This required me to manually ran the API multiple times and under various conditions in order to ensure that the software worked properly. A similar approach was undertaken to test the hardware. I regularly checked every part of the hardware to ensure that nothing was broken and that all pieces were installed correctly.
A simple logger was implemented to facilitate debugging.

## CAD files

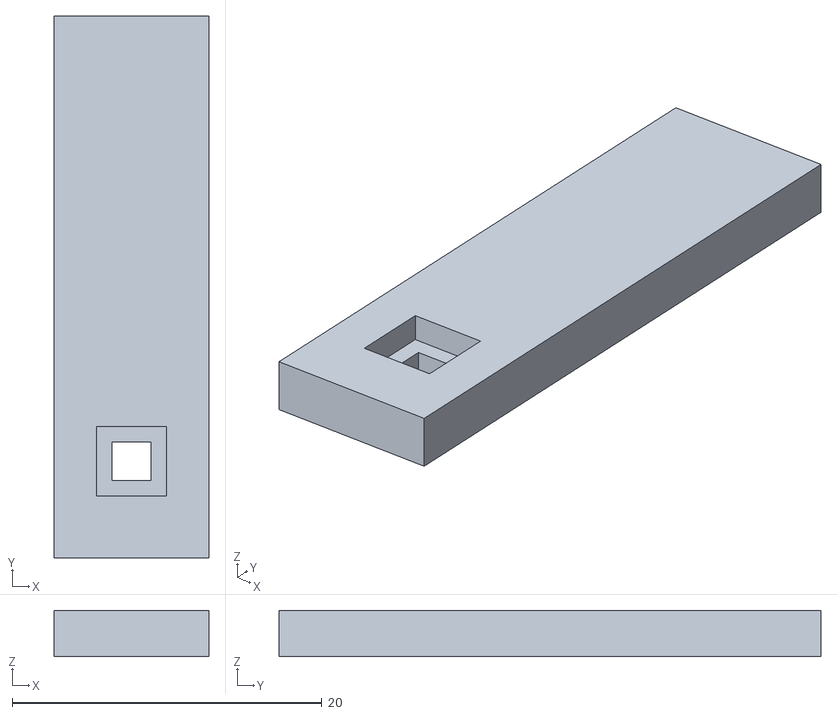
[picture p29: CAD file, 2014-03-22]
HaptiQ 3D Models/4-MHTP/Actuators/Actuator.stl
10.0 x 35.0 x 3.00

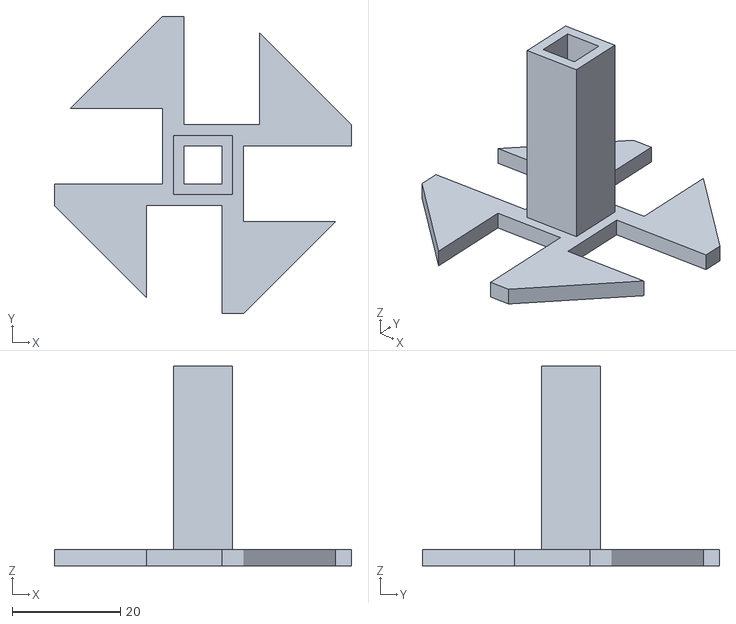
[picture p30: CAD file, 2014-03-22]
HaptiQ 3D Models/4-MHTP/Reference Actuator/reference-Type2.stl
55.0 x 55.0 x 37.0

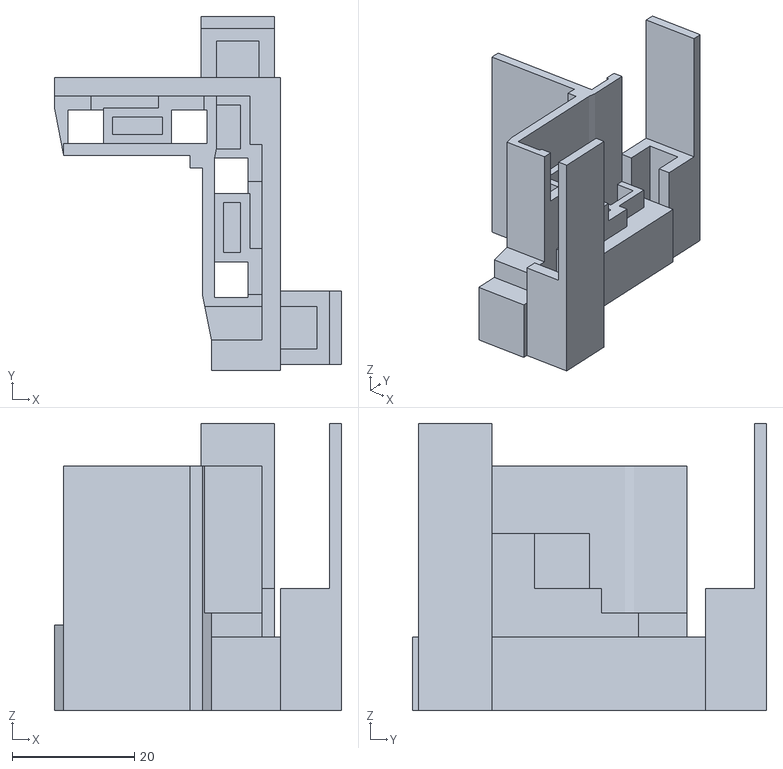
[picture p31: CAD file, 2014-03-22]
HaptiQ 3D Models/8-MHTP/Actuators Slots/prototype2.stl
47.0 x 58.0 x 47.0

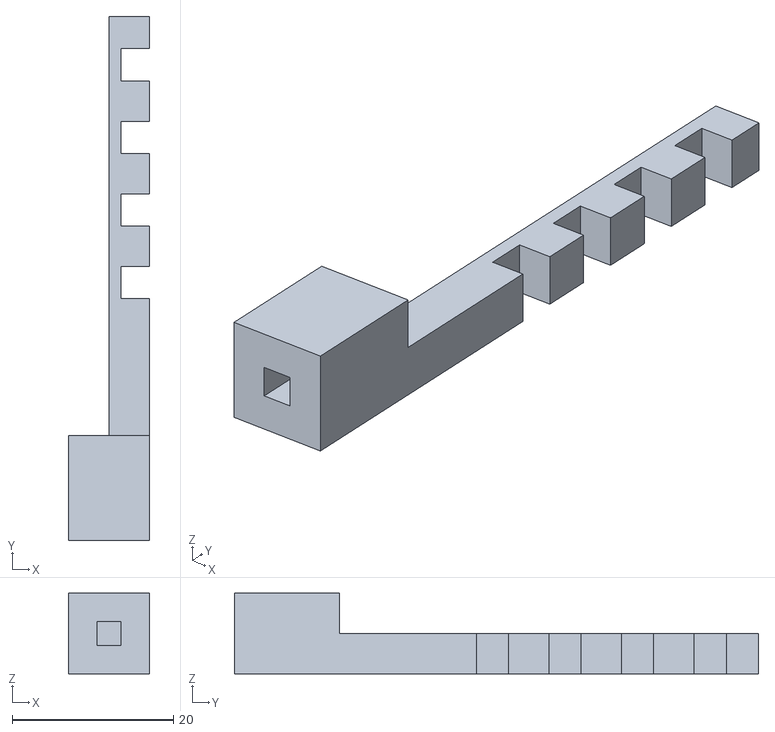
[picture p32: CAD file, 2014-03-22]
HaptiQ 3D Models/8-MHTP/Actuators/rod-Type1.stl
10.0 x 65.0 x 10.0

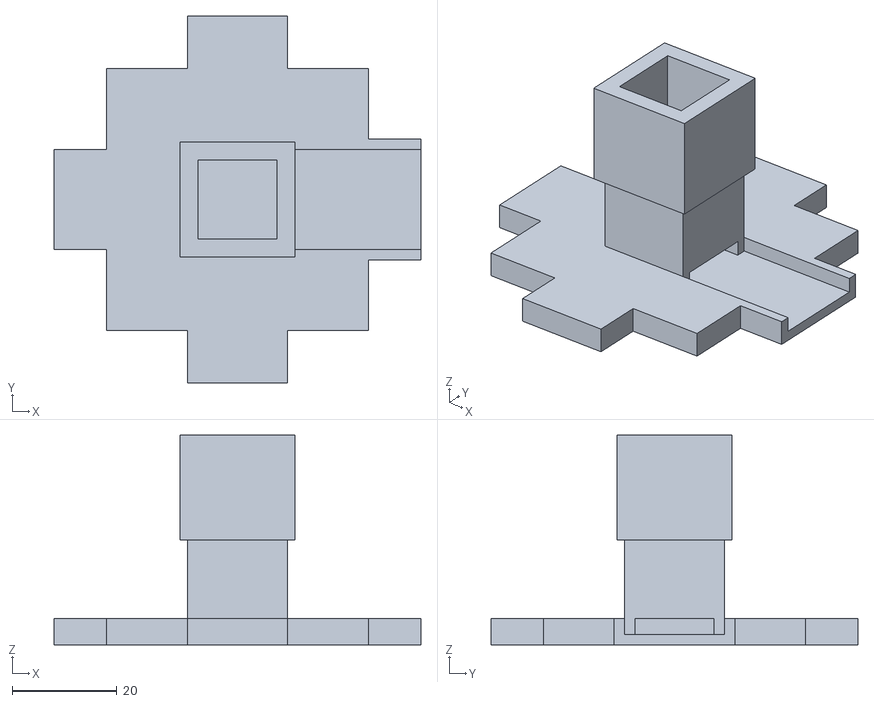
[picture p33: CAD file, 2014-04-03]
HaptiQ 3D Models/8-MHTP/Base/base.stl
70.0 x 70.0 x 40.0

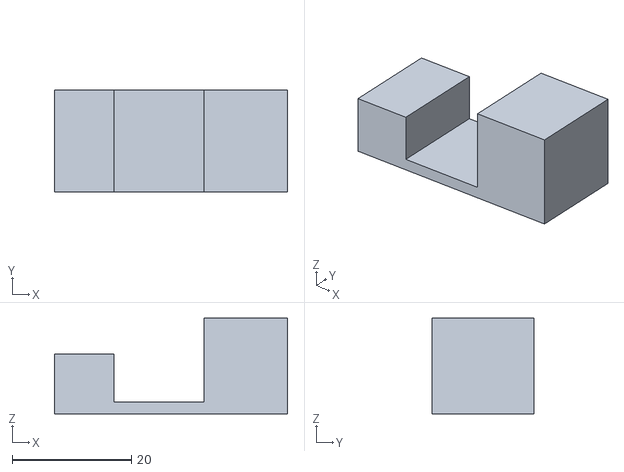
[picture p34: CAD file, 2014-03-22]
HaptiQ 3D Models/8-MHTP/Servos slots/base prototype.stl
39.0 x 17.0 x 16.0

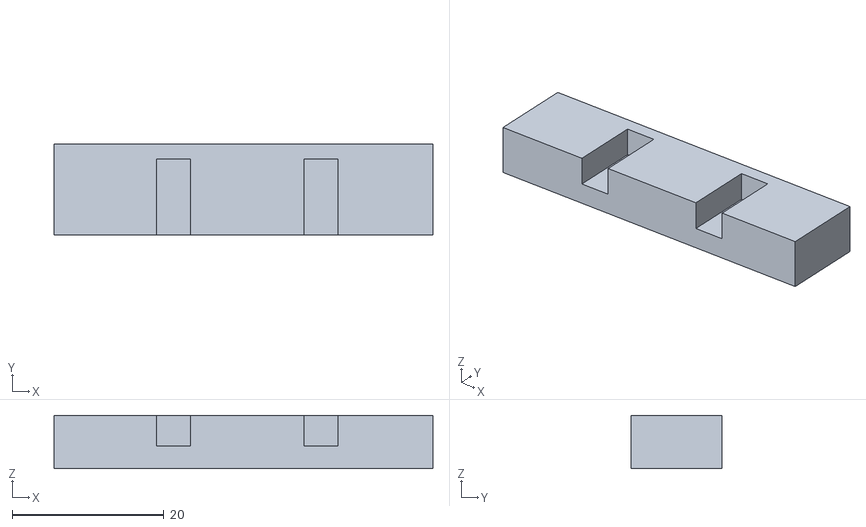
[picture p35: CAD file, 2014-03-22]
HaptiQ 3D Models/4-MHTP/Actuators/Top.stl
50.0 x 12.0 x 7.00

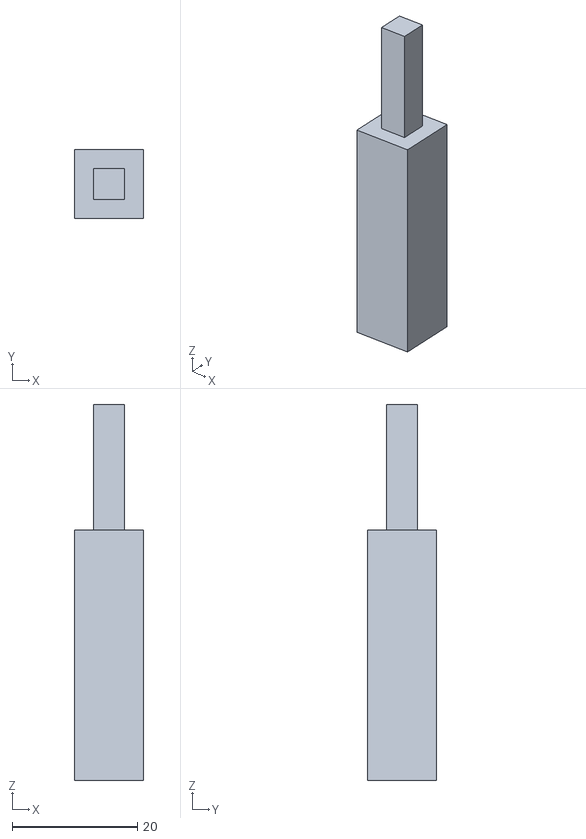
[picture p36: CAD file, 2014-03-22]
HaptiQ 3D Models/4-MHTP/Reference Actuator/reference-Type1.stl
11.0 x 11.0 x 60.0

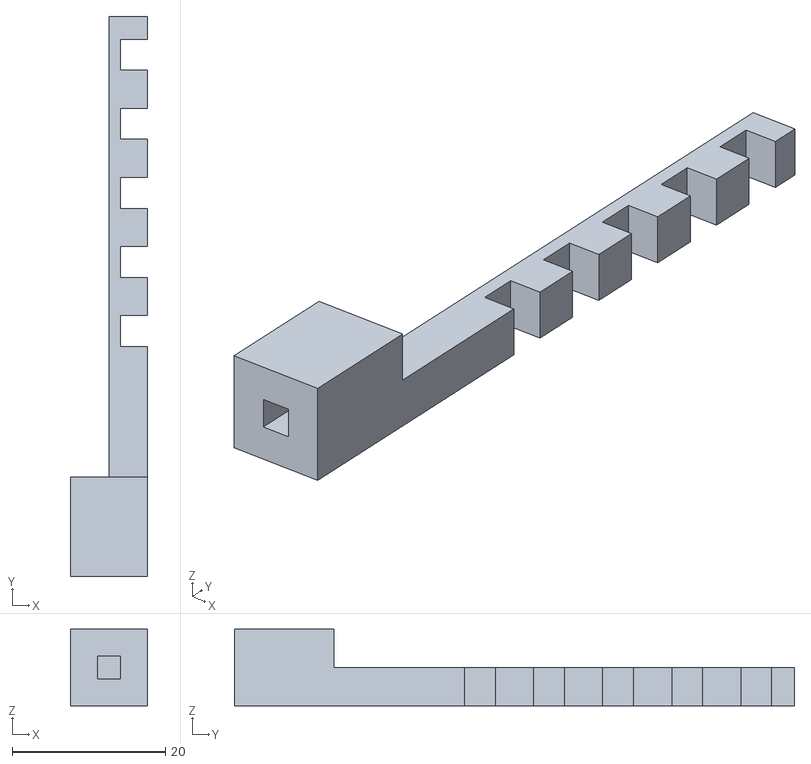
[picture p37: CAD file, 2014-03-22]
HaptiQ 3D Models/8-MHTP/Actuators/rod-Type2.stl
10.0 x 73.0 x 10.0

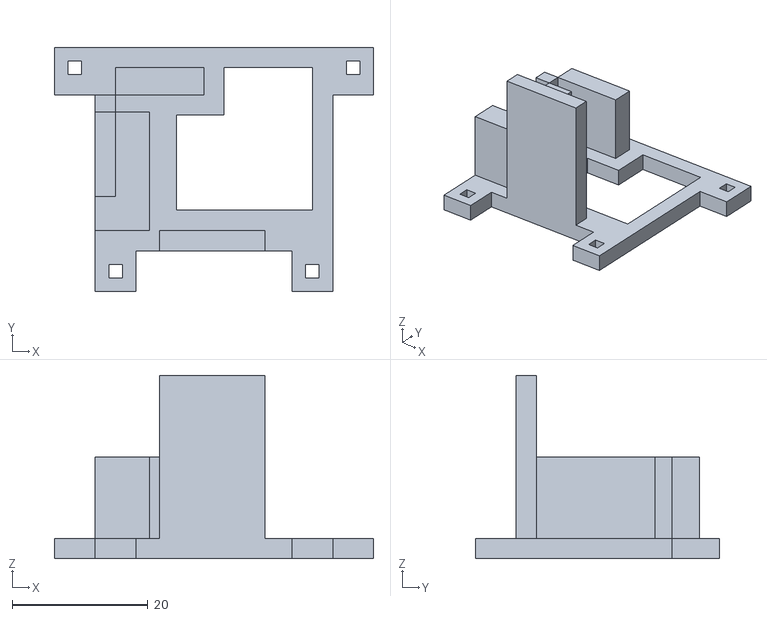
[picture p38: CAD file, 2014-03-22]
HaptiQ 3D Models/8-MHTP/Servos slots/topSide.stl
47.0 x 36.0 x 27.0

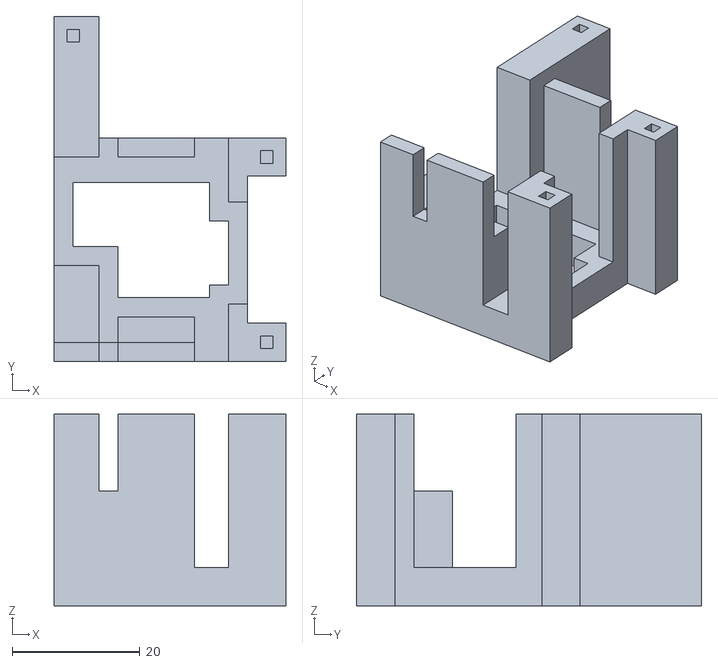
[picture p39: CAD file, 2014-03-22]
HaptiQ 3D Models/8-MHTP/Servos slots/support_larger.stl
36.3 x 54.0 x 30.0

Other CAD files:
HaptiQ 3D Models/4-MHTP/Actuators/Actuator.skp
HaptiQ 3D Models/4-MHTP/Actuators/Top.skp
HaptiQ 3D Models/4-MHTP/Plastic screw/support rotatory.skp
HaptiQ 3D Models/4-MHTP/Reference Actuator/reference-Type1.skp
HaptiQ 3D Models/4-MHTP/Reference Actuator/reference-Type2.skp
HaptiQ 3D Models/4-MHTP/Servo slot/servoSupport_2.skp
HaptiQ 3D Models/8-MHTP/Actuators Slots/prototype2.skp
HaptiQ 3D Models/8-MHTP/Actuators/rod-Type1.skp
HaptiQ 3D Models/8-MHTP/Actuators/rod-Type2.skp
HaptiQ 3D Models/8-MHTP/Base/base.skp
HaptiQ 3D Models/8-MHTP/Servos slots/base prototype.skp
HaptiQ 3D Models/8-MHTP/Servos slots/support_larger.skp
HaptiQ 3D Models/8-MHTP/Servos slots/topSide.skp

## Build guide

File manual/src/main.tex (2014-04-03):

\documentclass[a4paper]{article}

\usepackage[english]{babel}
\usepackage[utf8]{inputenc}
\usepackage{amsmath}
\usepackage{graphicx}
\usepackage{caption}
\usepackage{subcaption}
\usepackage[colorinlistoftodos]{todonotes}

\usepackage{hyperref}
\hypersetup{
    colorlinks,
    citecolor=black,
    filecolor=black,
    linkcolor=black,
    urlcolor=black
}

\graphicspath{{./}}

% Allow C# Code to be embedded
\usepackage{listings}
\usepackage{xcolor}
\usepackage{setspace}
\renewcommand{\lstlistingname}{Code}

\lstdefinestyle{sharpc}
{language=[Sharp]C, 
frame=single, 
rulecolor=\color{blue!80!black}, 
keywordstyle=\color{blue}, 
numbers=left,
breaklines=true,
basicstyle=\footnotesize\singlespacing}

\lstdefinestyle{sharpc1}
{language=[Sharp]C, 
frame=single, 
rulecolor=\color{blue!80!black}, 
keywordstyle=\color{blue}, 
numbers=none,
breaklines=true,
basicstyle=\footnotesize\singlespacing}

\definecolor{gray}{rgb}{0.4,0.4,0.4}
\definecolor{darkblue}{rgb}{0.0,0.0,0.6}
\definecolor{cyan}{rgb}{0.0,0.6,0.6}

\lstset{
frame=single, 
rulecolor=\color{blue!80!black}, 
breaklines=true,
  basicstyle=\ttfamily,
  columns=fullflexible,
  showstringspaces=false,
  commentstyle=\color{gray}\upshape
}

\lstdefinelanguage{XML}
{
  morestring=[b]",
  morestring=[s]{>}{<},
  morecomment=[s]{<?}{?>},
  stringstyle=\color{black},
  identifierstyle=\color{darkblue},
  keywordstyle=\color{cyan},
  morekeywords={xmlns,version,type}% list your attributes here
}

\title{HaptiQ Manual}

\author{Simone Ivan Conte \\\href{mailto:sic2@st-andrews.ac.uk}{sic2@st-andrews.ac.uk}}

\begin{document}
\maketitle

\newpage

\tableofcontents
\newpage

\section{Introduction}

This manual explains how to create WPF applications using the HaptiQ API and how to print the HaptiQ devices. \\
For further information or help, please contact the author of this manual.

\section{API}

This section will explain how to create a basic WPF application using the HaptiQ API. 

\subsection{Create a simple WPF project}

\begin{enumerate}
\item Creating a WPF (or Surface WPF) project as shown in Figure ~\ref{fig:createProj}. 

\item Add a reference of the \textit{HaptiQ\_API.dll} to the project. In Visual Studio:

\textit{$ Project \rightarrow Add Reference \rightarrow Browse $} (see Figure ~\ref{fig:addref}).

\item Use the following template in the \textit{XAML} view to get the input of the HaptiQ correctly (aligned with window):

\lstset{language=XML}
\begin{lstlisting}
<s:SurfaceWindow x:Class="TestApplication.SurfaceWindow1"
    xmlns="http://schemas.microsoft.com/winfx/2006/xaml/presentation"
    xmlns:x="http://schemas.microsoft.com/winfx/2006/xaml"
    xmlns:s="http://schemas.microsoft.com/surface/2008"
    Title="TestApplication"
                  mc:Ignorable="d"
                 xmlns:d="http://schemas.microsoft.com/expression/blend/2008" 
                 xmlns:mc="http://schemas.openxmlformats.org/markup-compatibility/2006" 
                 SizeToContent="WidthAndHeight"
    >
    <Grid  Name="Container" Height="700" Width="1000">

  </Grid>
</s:SurfaceWindow>
\end{lstlisting}

The name and size of the container are arbitrary values. 

\item Within the code view add the following line of code to start using the API:
\lstset{style=sharpc1}
\begin{lstlisting}
using HaptiQ_API; 
\end{lstlisting}

\item To start the HaptiQsManager:
\lstset{style=sharpc1}
\begin{lstlisting}
 HaptiQsManager.Create(this.Title, "SurfaceInput");
\end{lstlisting}

Change \textit{SurfaceInput} with \textit{SurfaceGlyphsInput} to use glyphs rather than bytetags

\item Always remember to dispose the HaptiQsManager and its resources. This is usually done in the OnClosed method of the WPF Window:

\lstset{style=sharpc1}
\begin{lstlisting}
protected override void OnClosed(EventArgs e)
        {
            base.OnClosed(e);
            RemoveWindowAvailabilityHandlers();

            HaptiQsManager.Instance.delete();
            Application.Current.Shutdown();
        }
\end{lstlisting}

\item Add Shapes where and when appropriate as follows:
\lstset{style=sharpc1}
\begin{lstlisting}
HapticShape shape = CREATE HAPTIC SHAPE
shape.color(Brushes.Brown);
Container.Children.Add(shape);
\end{lstlisting}

\end{enumerate}

\begin{figure}[H]
  \centering
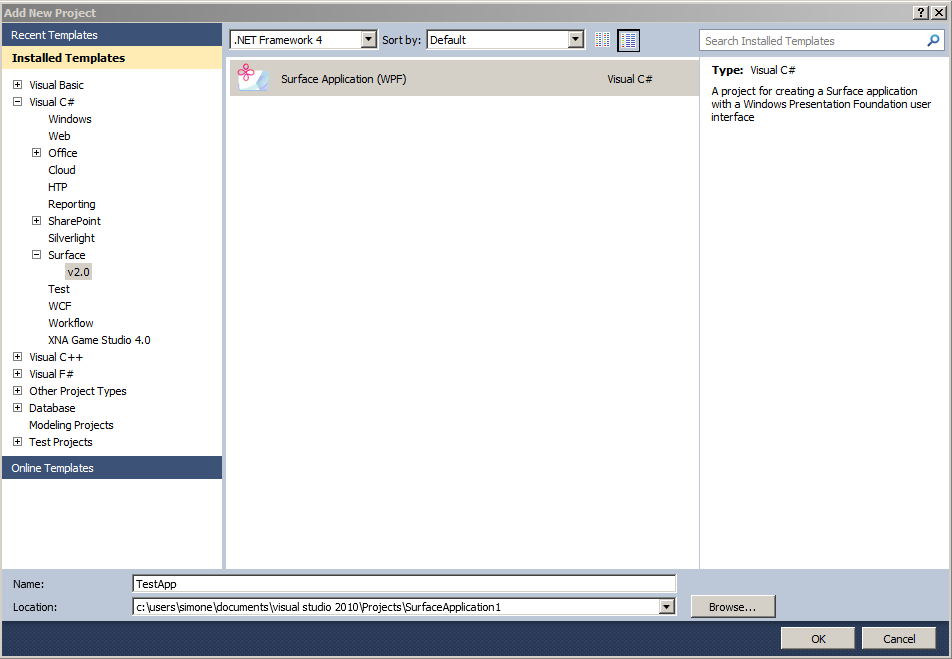
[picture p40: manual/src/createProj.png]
  
  \caption{Create a WPF project}
  \label{fig:createProj}
\end{figure}

\begin{figure}[H]
  \centering
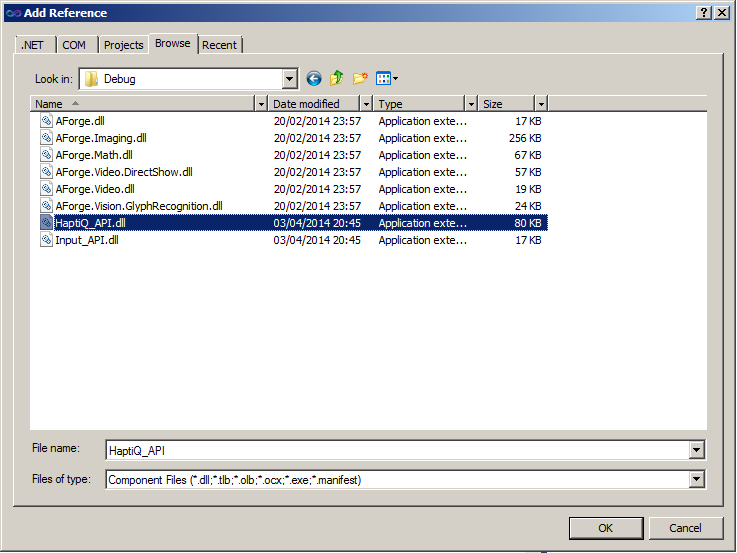
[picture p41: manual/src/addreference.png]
  
  \caption{Add reference to HaptiQ API}
  \label{fig:addref}
\end{figure}

The API contains a multitude of functionality. For more information it is suggested to use Visual Studio, which allows easy access to the documentation for the API. 

\subsection{HapticShapes}

The API supports the following HapticShapes:

\begin{itemize}
\item Rectangle
\lstset{style=sharpc1}
\begin{lstlisting}
HapticShape rectangle = new HapticRectangle(x, y, width, height);
\end{lstlisting}

\item Circle
\lstset{style=sharpc1}
\begin{lstlisting}
HapticShape circle = new HapticCircle(x, y, radius);
\end{lstlisting}

\item Link
\lstset{style=sharpc1}
\begin{lstlisting}
HapticShape link = new HapticLink(src, dst, linkHasDirection);
\end{lstlisting}

\item Line
\lstset{style=sharpc1}
\begin{lstlisting}
HapticShape line = new HapticLine(new Point(x, y), new Point(x_1, y_1));
\end{lstlisting}

\item Polyline
\lstset{style=sharpc1}
\begin{lstlisting}
List<Point> points = new List<Point>();
points.Add(new Point(x, y));
...
HapticShape polyline = new HapticPolyline(points);
\end{lstlisting}

\end{itemize}

HapticShapes are created for WPF applications. However, client applications can implement the \textit{IHapticObject} interface to support tactile objects for XNA application as well.

\subsection{Extending the API}

The API provided does not consider all possible types of applications users may want to implement. However, it is possible to extend it to add new functionality. The user can extend the API from the client side without having to modify the API. 

Note that it might be necessary to add a reference to the \textit{Input\_API.dll} when extending HapticShape.

\newpage
\section{Hardware}

The models for the 4-HaptiQ and the 8-HaptiQ can be found in the folder \textit{HaptiQ 3D Models}. Use MakerWare to import the STL files and print all the interested parts. Note that the printing can take up to several hours, based on the 3D printer used. 

\subsection{Hardware needed}

\begin{itemize}
	\item 3D Printer with 1.8mm ABS Plastic or equivalent
    \item 4 Hitech HS-65MG micro servomotors (8 for the 8-HaptiQ)
    \item 1 Phidget AdvancedServoBoard
    \item 1 Phidget InterfaceKit 8/8/8 or equivalent (must support analog input)
    \item 4 Force-Sensing resistors (8 for the 8-HaptiQ)
    \item Screws of various dimensions 
    \item Super glue
    \item Female and male crimps (with slots)
\end{itemize}

\section{Software Listing}

The software used in this project is listed below:

\begin{center}
    \begin{tabular}{ | l | p{3cm} | p{8cm} |}
    \hline
    Software & Description & Available at \\ \hline
    Phidget libraries & Control servos and pressure sensors & http://www.phidgets.com/ \\ \hline
    GRATF & Locate and recognize Glyphs & http://www.aforgenet.com/projects/gratf/ \\ \hline
    Glyphs Studio & Print Glyphs & http://www.aforgenet.com/projects/gratf/ \\ \hline
    Surface SDK 2.0 & Interface with tabletop & http://www.microsoft.com/en-gb/download/details.aspx?id=26716 \\ \hline
    NCalc & Evaluate mathematical functions in FunctionsApp & http://ncalc.codeplex.com/ \\ \hline
    VS2012 & C\# IDE & \- \\ \hline
    MakerWare & 3D Printer Software & https://www.makerbot.com/makerware/ \\ \hline
    SketchUp & 3D Modelling tool & http://www.sketchup.com/ \\ \hline
    SketchUp STL & STL Exporter plugin & http://extensions.sketchup.com/en/content/sketchup-stl \\ \hline
    \end{tabular}
\end{center}

\end{document}

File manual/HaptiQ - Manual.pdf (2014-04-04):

# HaptiQ Manual

Simone Ivan Conte
sic2@st-andrews.ac.uk

April 4, 2014

1

## Contents

1 Introduction | 3
2 API | 3
3 Hardware | 6
4 Software Listing | 6

2

## 1 Introduction

This manual explains how to create WPF applications using the HaptiQ API and how to print the HaptiQ devices.
For further information or help, please contact the author of this manual.

## 2 API

This section will explain how to create a basic WPF application using the HaptiQ API.

### 2.1 Create a simple WPF project

1. Create a WPF (or Surface WPF) project as shown in Figure 1.
2. Add a reference of the HaptiQ API.dll to the project. In Visual Studio: P roject → AddReference → Browse (see Figure 2).
3. Use the following template in the XAML view to get the input of the HaptiQ correctly (aligned with window):

<s:SurfaceWindow x:Class="TestApplication.SurfaceWindow1" xmlns="http://schemas.microsoft.com/winfx/2006/xaml/presentation"
xmlns:x="http://schemas.microsoft.com/winfx/2006/xaml"xmlns:s="http://schemas.microsoft.com/surface/2008"Title="TestApplication"
mc:Ignorable="d"
xmlns:d="http://schemas.microsoft.com/expression/blend/2008"
xmlns:mc="http://schemas.openxmlformats.org/markup-compatibility/2006"SizeToContent="WidthAndHeight"
>
<Grid Name="Container" Height="700" Width="1000">

</Grid>
</s:SurfaceWindow>

The name and size of the container are arbitrary values.

4. Within the code view add the following line of code to start using the API:

using HaptiQ API;

5. To start the HaptiQsManager:

HaptiQsManager.Create(this.Title, ”SurfaceInput”);

3

Change SurfaceInput with SurfaceGlyphsInput to use glyphs rather than bytetags

6. Always remember to dispose the HaptiQsManager and its resources. This is usually done in the OnClosed method of the WPF Window:

protected override void OnClosed(EventArgs e)
{
base.OnClosed(e);
RemoveWindowAvailabilityHandlers();

HaptiQsManager.Instance.delete(); Application.Current.Shutdown();
}
7. Add Shapes where and when appropriate as follows:

HapticShape shape = CREATE HAPTIC SHAPE shape.color(Brushes.Brown); Container.Children.Add(shape);

The API contains a multitude of functionality. For more information it is suggested to use Visual Studio, which allows easy access to the documentation for the API. The Templates contains an example that can be used as a starting point for a new application.

### 2.2 HapticShapes

The API supports the following HapticShapes:

- Rectangle

HapticShape rectangle = new HapticRectangle(x, y, width, height);

- Circle

HapticShape circle = new HapticCircle(x, y, radius);

- Link

HapticShape link = new HapticLink(src, dst, linkHasDirection);

- Line

HapticShape line = new HapticLine(new Point(x, y), new Point(x 1, y 1));

- Polyline

4

List<Point> points = new List<Point>(); points.Add(new Point(x, y));
HapticShape polyline = new HapticPolyline(points);

HapticShapes are created for WPF applications. However, client applications can implement the IHapticObject interface to support tactile objects for XNA application as well.

### 2.3 Extending the API

The API provided does not consider all possible types of applications users may want to implement. However, it is possible to extend it to add new functionality. The user can extend the API from the client side without having to modify the API.
Note that it might be necessary to add a reference to the Input API.dll when extending HapticShape.

5

## 3 Hardware

The models for the 4-HaptiQ and the 8-HaptiQ can be found in the folder HaptiQ 3D Models. Use MakerWare to import the STL files and print all the interested parts. Note that the printing can take up to several hours, based on the 3D printer used.

### 3.1 Hardware needed

- 3D Printer with 1.8mm ABS Plastic or equivalent
- 4 Hitech HS-65MG micro servomotors (8 for the 8-HaptiQ)
- 1 Phidget AdvancedServoBoard
- 1 Phidget InterfaceKit 8/8/8 or equivalent (must support analog input)
- 4 Force-Sensing resistors (8 for the 8-HaptiQ)
- Screws of various dimensions
- Super glue
- Female and male crimps (with slots)

## 4 Software Listing

The software used in this project is listed below:

Software | Description | Available at
Phidget libraries | Control servos and pressure sensors | http://www.phidgets.com/
GRATF | Locate and recog-nize Glyphs | http://www.aforgenet.com/projects/gratf/
Glyphs Studio | Print Glyphs | http://www.aforgenet.com/projects/gratf/
Surface SDK 2.0 | Interface with tabletop | http://www.microsoft.com/en-gb/download/details.aspx?id=26716 (http://www.microsoft.com/en-gb/download/details.aspx?id=26716)
NCalc | Evaluate mathe-matical functions in FunctionsApp | http://ncalc.codeplex.com/
VS2012 | C# IDE
MakerWare | 3D Printer Soft-ware | https://www.makerbot.com/makerware/
SketchUp | 3D Modelling tool | http://www.sketchup.com/
SketchUp STL | STL Exporter plu-gin | http://extensions.sketchup.com/en/content/sketchup-stl (http://extensions.sketchup.com/en/content/sketchup-stl)

6

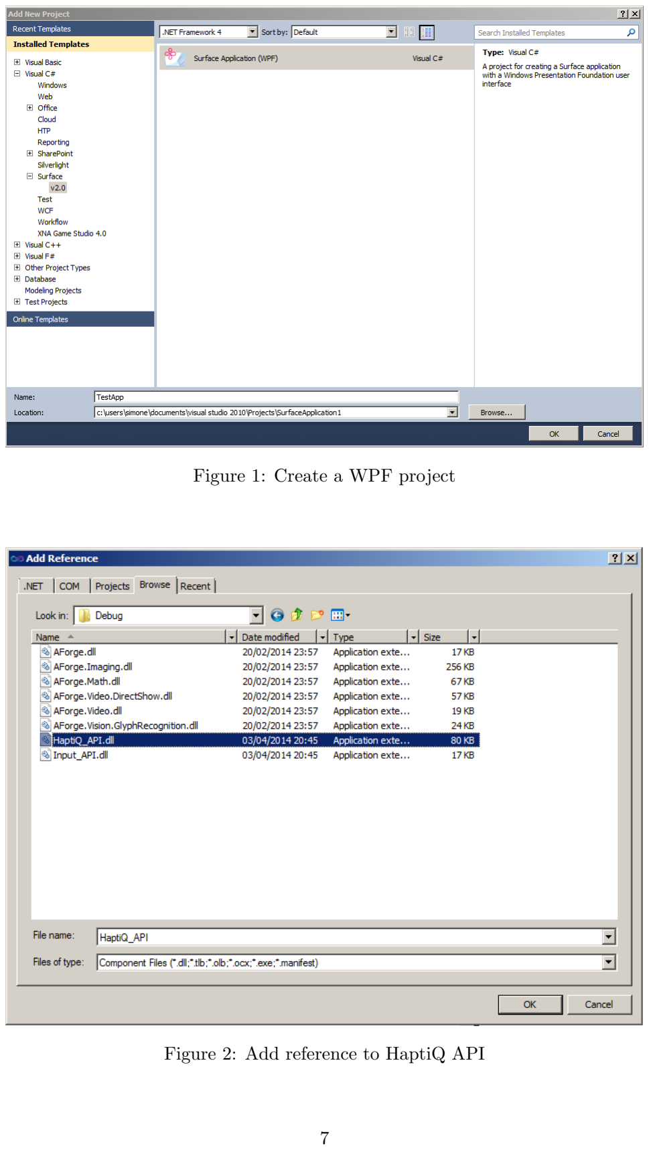
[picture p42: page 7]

Figure 1: Create a WPF project

Figure 2: Add reference to HaptiQ API

7

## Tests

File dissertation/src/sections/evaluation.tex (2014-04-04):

\chapter{Evaluation}

The project can be considered to have been successful, with all of the primary and secondary objectives achieved. Additional requirements, not included in the objectives, were also achieved. The project has evolved quickly and future work is already planned as discussed in Chapter ~\ref{chap:futureWork}. 

\section{The Hardware}

Designing and implementing the two HaptiQs has been a very challenging task. While the project is heavily inspired by the HTP \cite{marquardt2009haptic}, the device created in this project has been completely reinvented. The process of imagining 3D objects has been stimulating, but the low precision of the 3D printer transformed the entire process into a demanding one. This was particularly true for the first device, the 4-HaptiQ, due to the lack of experience with 3D modelling and printing. 

The miniaturization process of the 8-HaptiQ, added additional challenges. Assembling the second device, for instance, requires more time and precision. Some pieces, therefore, are not as easy to assemble as wanted. Nonetheless, being the HaptiQ only a prototype the focus has been more on creating a proof of concept, rather than a final product that can be produced in a short amount of time. One of the issues to solve, for example, is the position of the pressure sensors in the 8-HaptiQ. Currently, the sensors are placed on the outside of the actuators making the use of the device uncomfortable. 

No user study was conducted during this project. However, Saad, being visually impaired (he is one of the two collaborators, see Section ~\ref{sec:collaborators}), has provided some informal feedback on the first version of the device. He used a not fully working version of the 4-HaptiQ, with no pressure sensors, a Bytetag to locate the position of the device on the interactive table, and a point-reference actuator. The first note he made was about the point-reference actuator, which was disrupting the usability of the device. I also observed that even if the device did not work properly, he could still follow object edges with acceptable accuracy. The fact that tactons can be learned even with little or no practice is a positive feedback.   

I was unable to organize any other meetings with Saad to get feedback about the 8-HaptiQ. However, we plan to meet sometime in the near future to start working on the next iteration phase (see Chapter ~\ref{chap:futureWork}). 

The HaptiQ, similarly to the HTP, is intended to be inexpensive. The two prototypes created in this project have an estimated cost of circa £300.00. Using cheaper printed circuit boards, however, can lower the price to less than £100.00. This is a significant improvement over the current commercial technology (prices are usually over £1000.00).

\section{The API}

The structure of the API has changed few times, based on how the hardware evolved, the challenged faced and the new requirements that were introduced during the project. 
Initially, the API was designed to support input location via Bytetags only. However, glyphs had to be introduced to increase reliability and accuracy. In the month of February I was also told that Régis (he is one of the two collaborators, see Section ~\ref{sec:collaborators}) would join the project in March and that he will then use an interactive table not supporting the Microsoft Surface SDK 2.0. Therefore, I removed any dependency from the Surface SDK from the HaptiQ API and created a separate API to retrieve the input locations of the devices. 

The API has been designed and implemented to allow clients to easily use and possibly extend it. Régis has been using the API since the \nth{18} March 2014, without any major difficulties. He also played the role of the client in the project, by submitting issues about the project through GitHub. Some issues are still not solved, because not relevant to the objectives of this project. Other issues are simply not solvable due to technology limitations. For instance, at the moment it is not possible to define when a device is currently on the table or not. This is due to some inaccuracy issues of the GRATF library in recognising the glyphs and/or on the table providing raw images of low quality. A possible solution could be to classify a device as not being on the table whenever a glyph is not being recognised for more than a certain time threshold. 

The API supports basic pressure gestures recognition. The only gesture currently recognised is a press: the user applies high pressure on one of the actuators and then releases the finger or the palm. A drawback is that gestures can be recognised for single actuators only. It is also possible to detect more complex and interesting patterns by applying time-series analysis or using an hidden Markov model, but this is was outside the scope of this project. Figure ~\ref{fig:complexGesture} is an example of a more complex gesture, where checking values over the threshold might be misleading.

\begin{figure}[H]
  \centering
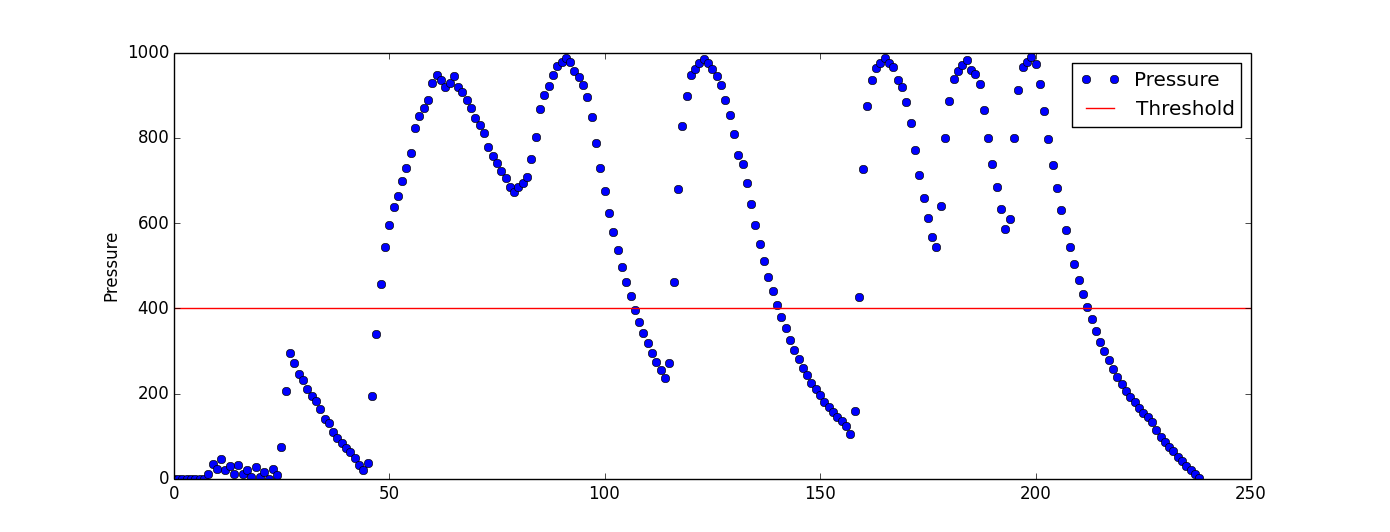
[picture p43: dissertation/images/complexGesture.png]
  
  \caption{Complex pressure gesture}
  \label{fig:complexGesture}
\end{figure}

\section{Tactons}

To the best of my knowledge, this work is the first to explore dynamic vector-based tactons to exploit haptic cues of edges, corners and directions. The tactons proposed by Pietrzak et al. \cite{pietrzak2009creating} are based on pin arrays. In his paper, it is interesting to note how the designed tactons evolved as user experiments were conducted. The tactons used for the HaptiQ, instead, are merely based on common sense rather than experimentation. Evaluating the current set of tactons and eventually producing a new improved set is part of the future work discussed in the next chapter.

During one of the meetings with Saad, we discussed a subset of the tactons presented in this report. His feedback was positive. The meeting after, when trying the HaptiQ, he was able to decode the behaviours efficiently. This cannot be considered a study of any kind, but his feedback was very valuable to define how the HaptiQ has evolved so far. 

\section{Applications}

The applications presented in this project function as proof of concepts only. Therefore, the applications can be improved largely. The graph visualiser, for example, could support the deletion of haptic objects and the possibility to save and load graphs for later uses. The functions visualiser, instead, can be of great help to students taking courses in mathematics both at school and university level. The application performs very well already, but there are still some issues with scaling and zooming to be solved. 

\section{Summary}

This project was very open-ended and consisted of many different components. Initially, I planned to conduct a user study to evaluate the HaptiQ. However, due to major ethical issues, I decided, with my supervisor, to focus more on the engineering aspects of the HaptiQ and its API. Nonetheless, an iterative process was used rather than a well structured one with well defined requirements. This allowed me to created two devices, with the second one completely re-engineered, and to evolve the API as needed.    

As previously stated, no user study has been conducted to formally evaluate the device.
The project, however, has been assisted and supervised throughout the whole design and implementation phases by Dr Miguel A. Nacenta, who is an expert in Human-Computer Interaction and haptic interfaces. The contribution of Dr Nacenta has been particularly fundamental to validate the design process of the hardware and the tactons.

Conclusions can also be drawn by comparing the device with the state of the art in haptic technology. \\
The HaptiQ, unlike MIMs \cite{brock2010usage} and inFORM \cite{follmer2013inform}, can be used on any interactive surface as long as it is possible to track the device. The HaptiQ, for example, can be used on a normal paper map assuming a top-down tracking mechanism is provided. This makes the HaptiQ more flexible and less expensive, since it can be reused in different scenarios.\\
TeslaTouch \cite{bau2010teslatouch} and REVEL \cite{bau2012revel} allow users to perceive tactile cues extrinsically or intrinsically. Both of these systems allow users to feel texture and to follow lines. The HaptiQ uses a variety of tactons to indicate not only lines, but directions as well. In addition, electrovibration or vibrational mechanical motors can be integrated with the HaptiQ to allow textures to be sensed. \\
UltraHaptics \cite{carter2013ultrahaptics} and AIREAL \cite{sodhi2013aireal} provide haptic feedback in a 3D environment. Accuracy, in these systems, is not constant in space. These solutions, in fact, tend to use tactile feedback for media applications to be used by the visually impaired, rather than by blind people. 

Finally, a brief discussion about the objectives that were not achieved is needed. \\
Initially, one of the secondary objectives was to allow dynamic pointing on the interactive surface. But people with visual disabilities may encounter difficulties on keeping track of the relative position of a dynamic pointer, since no visual feedback can be perceived. Therefore, this objective was discarded. \\
The tertiary objectives included: enabling the haptic device to be used collaboratively and allowing the device to sense textures. 
With the focus of the project being on the tactile cues that the HaptiQ could enhance, I decided to give lower priority to any possible feature that could allow communication between two devices. However, the API can support multiple devices. Thus, clients can implement  collaborative features on top of the API.
On the other hand, the objective of adding the possibility to sense texture was not attempted because the frequency at which the servos, used for this project, work is too low \cite{brown2005first}. A possible alternative could be to add a central static actuator to the devices, similar to the point-reference actuator, which could convey texture information to users via electrovibration \cite{bau2012revel, bau2010teslatouch} or mechanical vibration \footnote{Example of vibration motor for haptic feedback available at \url{http://www.precisionmicrodrives.com/vibrating-vibrator-vibration-motors}. [Online; last checked: 04/04/2014].}.

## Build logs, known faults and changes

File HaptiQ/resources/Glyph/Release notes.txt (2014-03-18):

GRATF 2.0.1 release notes
------------------------------
06.03.2012.

Version updates and fixes:

* The project is updated to use AForge.NET framework version 2.2.4.1.

* The project is updated to use Visual Studion .NET 2010 (C# Express Edition 2010 is fine to use).

* The project is updated to use XNA 4.0.

GRATF 2.0.0 release notes
------------------------------
19.09.2011.

Version updates and fixes:

* The project is updated to use AForge.NET framework version 2.2.2

* Glyph recognition/tracking library
  - Added glyph tracking class, which tracks glyphs throughout a video stream.
    While tracking it takes care of glyphs' "shaking" - suppresses noise in
    detection of glyphs' corners (if any of corners' coordinates don't change
    for more than one pixel, then corners' coordinates are taken from previous
    video frame). Also the class does glyphs' pose estimation using Coplanar
    POSIT algorithm from AForge.Math namespace.

* Glyph Recognition Studio
  - Added possibility to print glyphs from the application.
  
  - Added XNA based visualizer of 3D augmented reality. It puts 3D object on top
    of a recognized glyph using same pose as the glyph has.

GRATF 1.0.0 release notes
------------------------------
05.11.2010.

First release of the project. Based on AForge.NET framework v.2.1.4

It includes:

- A prototype of glyph recognition algorithm, which is implemented as a
  plug-in to IPPrototyper tool from AForge.NET framework. Can be used
  for demonstrating glyph recognition algorithm's idea step by step or
  for its further improvement, debugging and testing.
  
- Glyph Recognition Studio - an application which does recognition of glyphs
  in video streams (video files or local capture devices, like web cameras).
  Also the application does 2D augmented reality - puts images into video
  feed replacing recognized glyphs - virtual objects in real world.

- Glyph recognition library, which is an extension to AForge.NET framework.
  The library can be reused in other applications which require glyph
  recognition functionality.

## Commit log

2014-03-18 moving from HG to GIT
    [pressure base male.skp, pressure base male.stl, pressure base.skp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]
2014-03-20 Added possibility to subscribe to position and pressure events both from the MHTPsManager and/or each individual MHTP.
2014-03-20 behaviours use relative actuators positions
2014-03-20 Initialise pressure value for actuators. Fixes #2
2014-03-20 added event for actuators position changes
2014-03-21 Fixed issue with windowHandle not being correctly initialised Catching exceptions if a servo is not attached Fixed issue with point-to-segment distance Fixed issue with behaviours changing
2014-03-22 3D Models
    [Actuator.skp, Actuator.stl, Top.skp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]
2014-03-22 remove duplicate files
    [pressure base male.skp, pressure base male.stl, pressure base.skp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]
2014-03-23 Fixed issue with actuator not disabling correctly on MHTP disposing
2014-03-23 - restricted setHeight methods in Actuator class - added setHeightByPercentage methods in MHTP class - changed behaviours to use percentage, so that these work on any MHTP device
2014-03-23 Allow hapticShapes t support multiple devices Fixed minor issue about BasicBehaviour
2014-03-24 Use pressure data in basic behaviours
2014-03-25 Changed title of the dissertation to: HaptiQ: A Haptic Device for Graph and Text exploration by People with Visual Disabilities started working on Design chapter
2014-03-26 new feature: Actions.
    These are used when relevant pressure input is received.
2014-03-26 Fixed issue with handling HapticShapes states for different devices
2014-03-28 Replacing all occurrences of MHTP with HaptiQ
    [Actuator.skp, Actuator.stl, Top.skp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]
2014-04-02 Fix configuration issue with retrieving all config-xml files from current directory.
    Plus pressure progress bars in HaptiQ configuration form were not in the right order
2014-04-03 base 3d model for the 8-HaptiQ
    [base.skp, base.stl]
2014-04-09 repo cleanup and minor fixes:
    fixed issue with multiple configurations
    fixed issue with actuators being static
